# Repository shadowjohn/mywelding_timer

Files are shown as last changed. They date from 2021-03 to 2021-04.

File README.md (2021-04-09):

# mywelding_timer
<h2>功能：</h2>
　　微波爐變壓器改裝可調時間點焊機
<br>
<br>
作者：羽山秋人 (https://3wa.tw)<br>
<br>
最初開發日期：2021-03-27 12:05<br>
最後更新日期：2021-04-02 21:53<br>
版本：V0.1<br>
License：MIT<br>
<br>
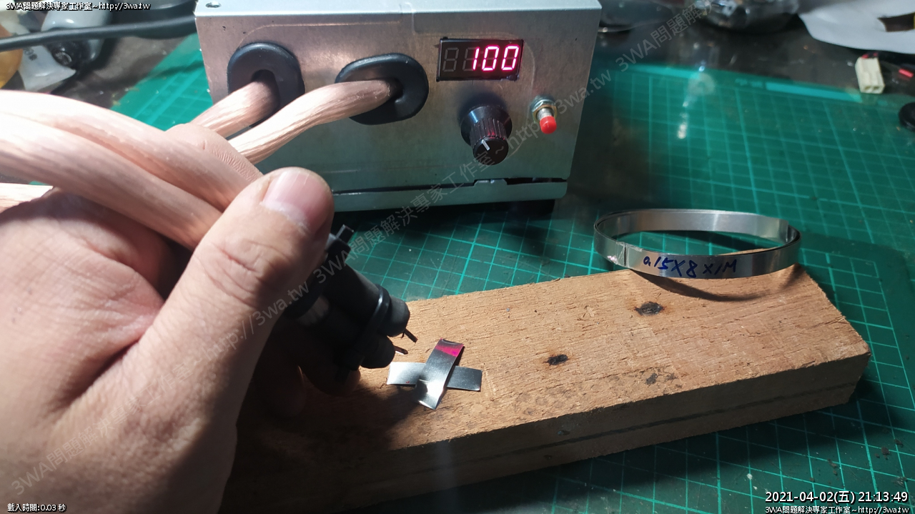
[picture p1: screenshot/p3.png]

<br>
~~~自製點焊機成功~~~
<img src="screenshot/p4.png">
<br>
可調時間點焊機
<h2>說明：</h2>
　　羽山在 Youtube 上看到好多老外都用「微波爐變壓器」把細的線圈拆掉後，換上粗電線，繞個二圈，就可以作成 AC 110V to AC 1~2V 點焊機，拿來焊 18650 或其他鋰電池、鋰鐵電池、不銹鋼杯手柄，相當好用。<br>
　　前些日子買了一台中古的變壓器，試作成功，接下來要再作一個簡單的電路來精準控制焊接的時間，讓鎳片跟電池的焊接時間最佳化。<br>
　　此電路會偵測可變電阻的電阻值，將 10KΩ 轉成 50ms~1000ms，顯示在四位元七段顯示器上，此時按下「微動開關」就可以讓「繼電器Relay」打開讓交流電通過一段時間後再關上。<br>
　　搭配微波爐變壓器作成點焊機，即可控制點焊的時間，將來要焊電池、焊鎳片相當方便。
<br>
<h2>所需材料：</h2>
<ul>
  <li>微波爐變壓 800w x 1</li>
  <li>35平方軟銅線4尺</li>
  <li>鎳片/焊片各種規格</li>
  <li>粗銅線1.6mm x 7cm x 2，拆粗的單芯電線即可</li>
  <li>AC 110V TO DC 12V 變壓器(Nodemcu 供電用)</li>
  <li>YuRobot 545043 Buck x 1，或 LM2596 Buck x1 ，比較推薦用 LM2596</li>
  <li>20A 搖頭開關 x 1</li>  
  <li>Arduino ESP8266 x 1</li>
  <li>TM1637 4 Digital Display 四位元七段顯示器 x 1</li>
  <li>可變電阻 10KΩ x 1</li>
  <li>電阻 1KΩ 1/2w x 3</li>
  <li>電阻 330Ω 1/2w x 2</li>
  <li>電容 10㎌ 50V x 2</li>
  <li>LED 綠、紅 各一顆</li>
  <li>蜂嗚器 5V x 1</li>
  <li>Relay 5V x 1</li>
  <li>洞洞板 x 1</li>
  <li>微動開關 x 1</li>
  <li>二極體 1N4007 x 1</li>
</ul>
<h2>接腳說明：</h2>
<ul>
  <li>D0：TM1637 CLK</li>
  <li>D1：TM1637 DIO</li>
  <li>D2：RELAY 5V</li>
  <li>D3：微動開關 Input</li>
  <li>建議腳位可以設開一點，如 D0 D2 D4 D6，以免焊接時太近短路沒發現</li>
</ul>
<h2>使用注意事項：</h2>
<ul>
  <li>1. 燒錄程式前，請先將 3.3V 接 5V 的線拔除，或把 Nodemcu 燒好再接上此電路 (拔除後，電腦才能識別)</li>
  <li>2. (開機保護) 開機時，需按著「微動開關」再同時過電，才能正常開機 (D3 保持高電位才能正常開機 )</li>
  <li>3. (去彈跳功能)「微控開關」需壓 0.3 秒左右，才能焊接，放開後也要等 0.3 秒後再壓，才能焊下一個點</li>
</ul>
<h2>說明影片：</h2>
<ul>
  <li>影片一：<a target="_blank" href="https://youtu.be/TA6dgjnLMRM">https://youtu.be/TA6dgjnLMRM</a></li>
  <li>影片二（製作完成）：<a target="_blank" href="https://youtu.be/AywPSv3ZF3s">https://youtu.be/AywPSv3ZF3s</a></li>
</ul>
<h2>完整製作心得：</h2>
https://3wa.tw/blog/blog.php?id=1904
<h2>電路圖：</h2>
<center>
  <img src="Circuit_diagram/welding_timer.png">
</center>
<h2>手繪電路圖：</h2>
<center>
  <img src="screenshot/p1.png">
</center>
<h2>電路圖：</h2>
<center>
  <img src="Circuit_diagram/circuit_diagram.png">
</center>
<h2>麵包板測試：</h2>
<center>
  <img src="screenshot/p2.png">
</center>

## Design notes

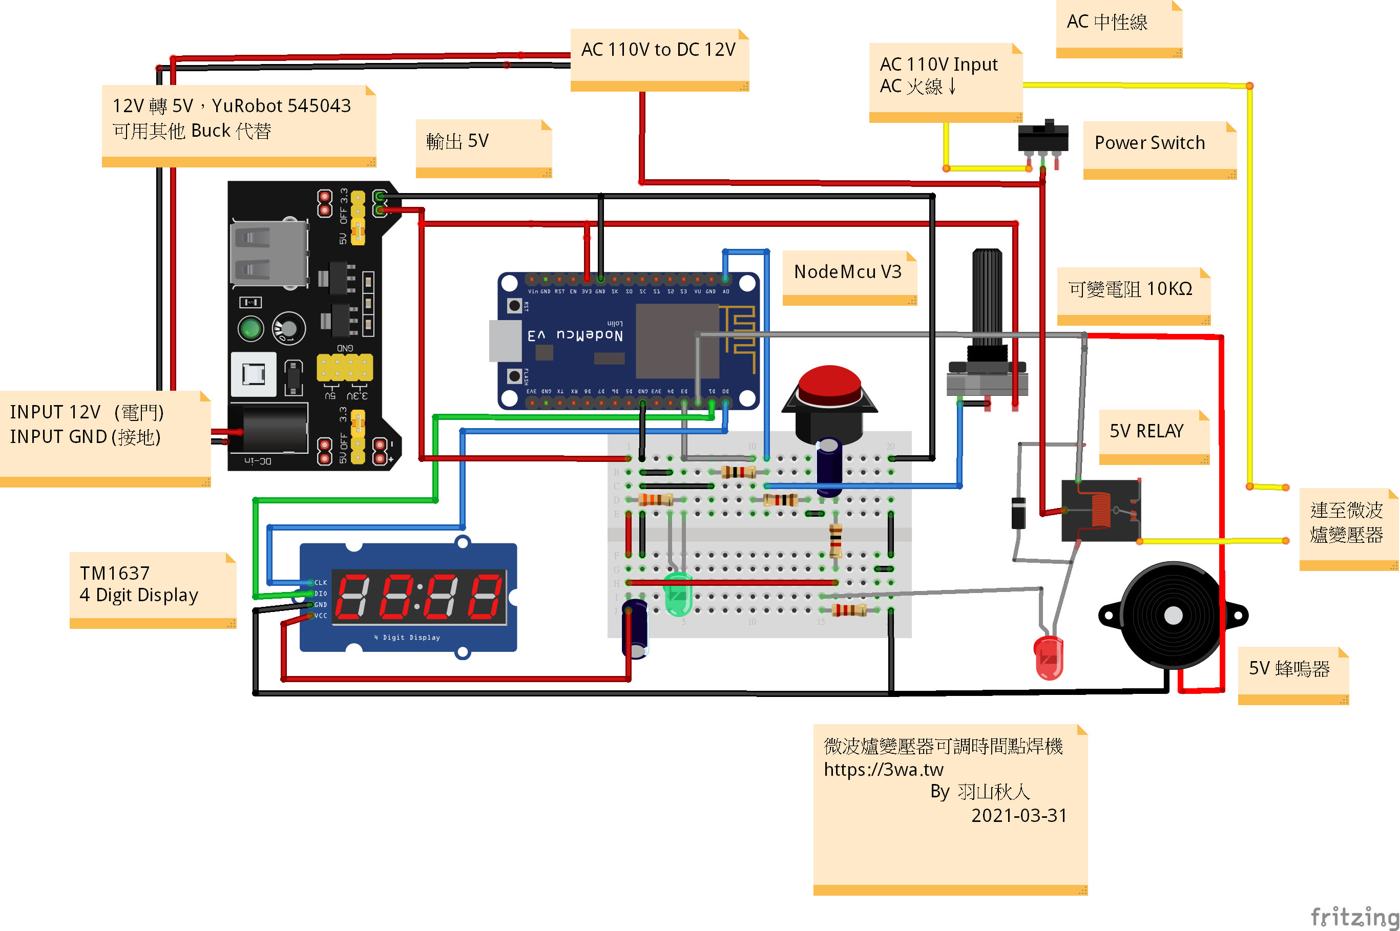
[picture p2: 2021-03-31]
Circuit_diagram/welding_timer.png

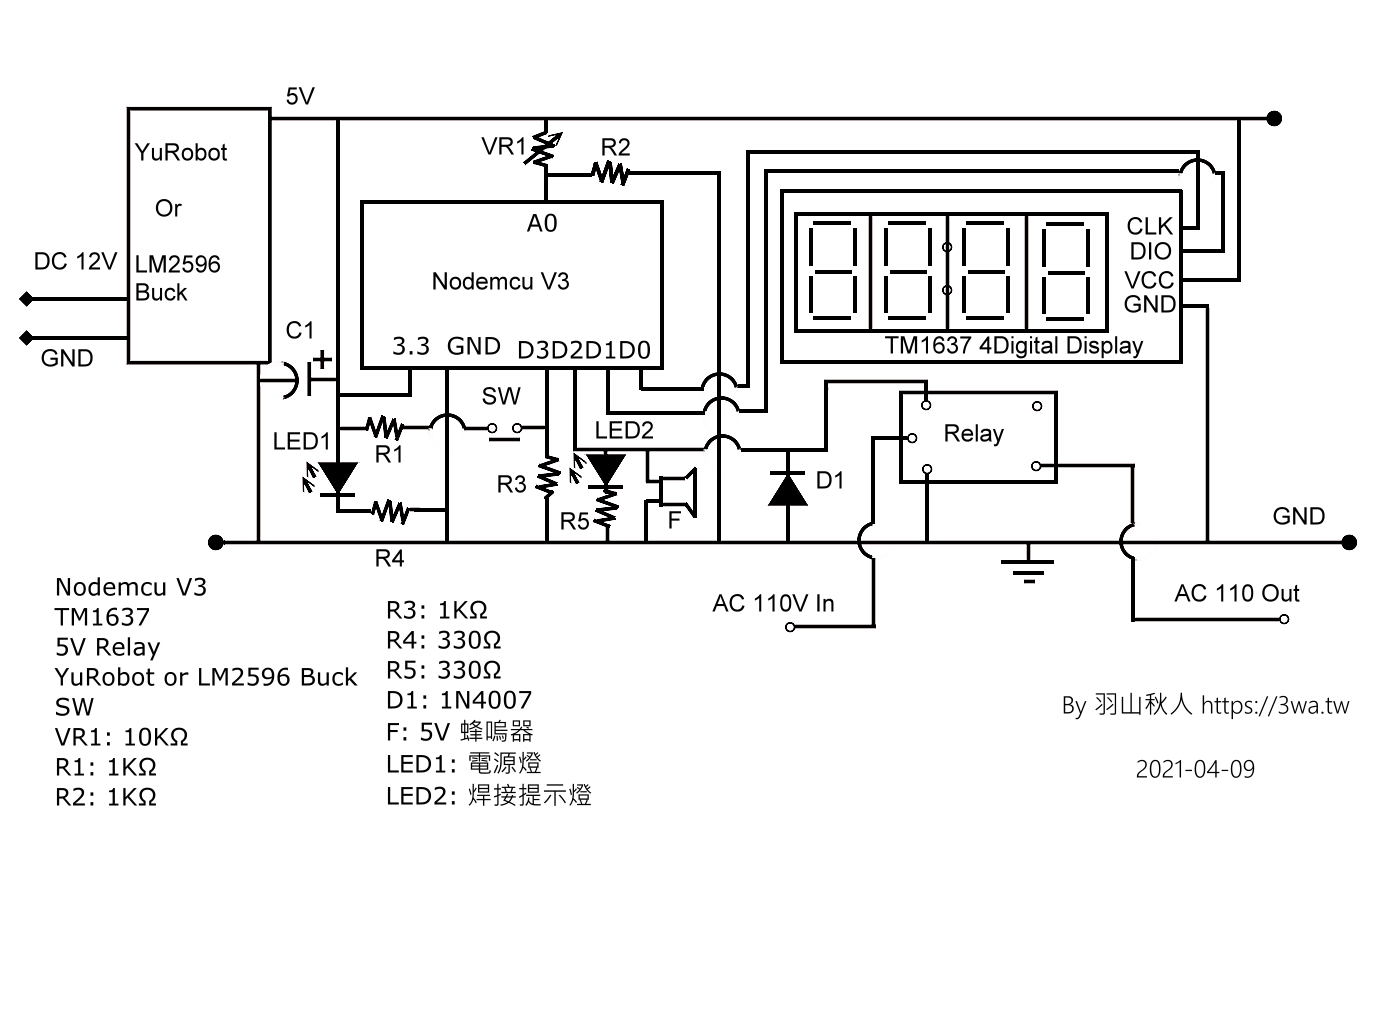
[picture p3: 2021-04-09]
Circuit_diagram/circuit_diagram.png

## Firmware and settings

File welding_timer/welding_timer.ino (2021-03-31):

/*
 * Welding Timer 焊接機 V0.1
 * Release Date: 2021-03-30
 * By 羽山秋人 (https://3wa.tw)
 * GitHub: https://github.com/shadowjohn/mywelding_timer
 * 
 * 接腳參考
   #define CLK D0   (TM1637 4 Digital Display)
   #define DIO D1   (TM1637 4 Digital Display)
   #define RELAY D2 (接焊接繼電器)
   #define BTN D3   (焊接按鈕)
   #define A0       (可變電阻)
*/
//get VCC Voltage
// From : https://www.reddit.com/r/esp8266/comments/9ubypi/how_do_i_use_the_espgetvcc_correctly/
//ADC_MODE(ADC_VCC)  
//int batterylevel;  

//數位模組 Grove_4Digital_Display
#include <TM1637.h>

#define CLK D0 //pins definitions for TM1637 and can be changed to other ports
#define DIO D1 //給 4 Digit-Display TM1637 使用
#define RELAY D2 //繼電器接角
#define BTN D3 //焊接按鈕
long steps = 0;
long steps_btn = 0;
int analogPin = A0;
int weldingTime = 50;
float R1 = 1000; //R1 是參考電阻 (1KΩ)
float R2 = 0; //記錄 可變電阻值，如 0Ω~10000Ω (0~10K)

TM1637 tm1637(CLK,DIO); //定義顯示器變數
//int sleep_step = 50; //最少，最多1000(ms) 50 100 150 200 ...
bool isUpClick = true; //是否曾放開按鈕
bool isBooting = true;
bool isWelding = false;
void setup() {
  // put your setup code here, to run once:
  Serial.begin(115200);   
  pinMode(RELAY,OUTPUT);  
  pinMode(BTN,INPUT); 
  digitalWrite(RELAY,LOW); //一開始不work
  // 4 Digit-Display
  tm1637.init();  
  tm1637.set(2); //BRIGHT_TYPICAL = 2,BRIGHT_DARKEST = 0,BRIGHTEST = 7;，數值越大，越亮
  //回歸零
  tm1637.display(0,-1); //-1 for blank
  tm1637.display(1,-1); //-1 for blank
  tm1637.display(2,-1); //-1 for blank
  tm1637.display(3,0);
}
void updateR2(){
  //取得目前可變電阻姿態，將電阻值存到 R2
  //batterylevel = ESP.getVcc();  
  //本來想用ESP.getVcc 來取得電壓，但一寫就當，幹
  int raw = analogRead(analogPin);
  float Vin = 5.0;//batterylevel /1000.0; //5.0;
  if(raw) 
  {
    float buffer= raw * Vin;
    //Serial.print("Vin:");
    //Serial.println(Vin);
    //Serial.print("raw:");
    //Serial.println(raw);  
    
    float Vout = (buffer)/1350.0; //1350 是常數嗎@_@?
    buffer= (Vin/Vout) -1;
    R2 = R1 * buffer;
    //Serial.print("Vout: ");
    //Serial.println(Vout);
    //Serial.print("R2: ");
    //Serial.println(R2);
    //delay(200);
    R2 = R2 - (int(R2) % 50); //55->50  132->100
  }
  
}
void diaplayOnLed(int show_rpm,bool fill_zero=false)
{
  //將轉速，變成顯示值
  //只顯示 萬千百十
  //如果要顯示 千百十個，就不用除了
  //太多數位有點眼花
  weldingTime = show_rpm;
  if(!isBooting)
  {    
    int lowV=2200;
    int maxV=7400;
    
    show_rpm = (show_rpm < lowV)?lowV:show_rpm;
    show_rpm = (show_rpm > maxV)?maxV:show_rpm;
    weldingTime = map(show_rpm, lowV, maxV, 50, 1000); 
    if( weldingTime != 50 )  
    {
      weldingTime = weldingTime -(weldingTime%100);
    }
  }
  weldingTime = (weldingTime<=50)?50:weldingTime;
  
  String rpm_str = String(weldingTime); //  /10
  if(rpm_str.length()<=3)
  {
    if(fill_zero==true)
    {
      rpm_str = lpad(rpm_str,4,"0"); // 變成如 "0000"
    }
    else
    {
      rpm_str = lpad(rpm_str,4,"X"); // 變成如 "XXX0"
    }
    
  }
  Serial.print("\nAfter lpad:");
  Serial.println(rpm_str);
  for(int i=0;i<4;i++)
  { 
      if(rpm_str[i]=='X')
      {
        tm1637.display(i,-1); //-1 代表 blank 一片黑    
      }
      else
      {
        // Serial.println(rpm_str[i]);
        // 腦包直接轉回 String 再把單字轉 int
        // From : https://www.arduino.cc/en/Tutorial.StringToIntExample
        tm1637.display(i,String(rpm_str[i]).toInt());    
      }
  }
}
String lpad(String temp , byte L , String theword){
  //用來補LED左邊的空白
  byte mylen = temp.length();
  if(mylen > (L - 1))return temp.substring(0,L-1);
  for (byte i=0; i< (L-mylen); i++) 
    temp = theword + temp;
  return temp;
}
void runTest(){
  //開機後，0000~9999 一次
  for(int i=0;i<=9999;i+=1111)
  {
    diaplayOnLed(i,true);
    delay(300);  
  }
  delay(300);    
  diaplayOnLed(0,false);
}

void loop() {
  /*batterylevel = ESP.getVcc();  
  if(batterylevel <= 2170){  
    Serial.print("\nBatterylevel: ");
    Serial.println(batterylevel);
    ESP.deepSleep(0);  
  }  
  Serial.print("\nBatterylevel:");
  Serial.println(batterylevel);
  */
  if(isBooting)
  {
    //開機自動run 0000~9999
    runTest();
    isBooting=false;
  }
  
  //updateR2();
  steps++;
  steps%=40000;
  if(steps==0)
  {
    //當step 為整數0，才detect 一次電阻顯示到 LED 就好
    updateR2();
    diaplayOnLed(int(R2),false); //顯示到 LED
  } 
  //偵測按鈕是否按下
  //Serial.print("\ndigitalRead(BTN):");
  //Serial.println(digitalRead(BTN));  
  //Serial.print("\nmillis()-steps_btn:");  
  //計數到 25000 才能執行一次焊接
  //25000是在作防按鈕彈跳
  steps_btn++;
  steps_btn = (steps_btn>=25000)?25000:steps_btn;
  
  //Serial.print("\nsteps_btn:");
  //Serial.println(steps_btn);
  //25000 是用來去除彈跳的寫法
  if( digitalRead(BTN) == HIGH && isUpClick == true && steps_btn >= 25000 )
  {
    //按下按鈕後，開始焊接
    isUpClick = false;
    isWelding = true; 
    digitalWrite(RELAY,HIGH); //焊接開始
    delay(weldingTime); 
    digitalWrite(RELAY,LOW);
    //Serial.println("Done Welding...");  
    //Serial.println("Done Welding...");  
    //Serial.println("Done Welding...");  
    isWelding = false;    
    steps_btn = 0;
  }
  if(digitalRead(BTN)==LOW)
  {
    //放開按鈕，計數器收置
    isUpClick = true;   
    steps_btn = 0;   
  }  
}

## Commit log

2021-03-30 更新 README.md
2021-03-30 去除readme 空白
2021-03-30 更新電路圖
    [welding_timer.fzz]
2021-03-31 更新程式碼與電路
    [welding_timer.fzz]
2021-03-31 補實作圖片
2021-04-01 更新手繪圖
2021-04-02 製作完成
2021-04-09 update Nodemcu circuit_diagram
